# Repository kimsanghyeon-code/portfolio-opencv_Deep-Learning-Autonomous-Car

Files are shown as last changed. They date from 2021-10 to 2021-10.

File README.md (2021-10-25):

# 신경망을 이용한 자율주행차 구현
<hr>
  <h1> 구현 세부 내용 </h1>
<ol>
  <li> 듀얼쇼크4 페어링 후 'DataCollectionMain.py'실행하여 도로주행 </li>
  <li> 'Training.py'실행하여 주행하며 촬영한 이미지를 데이터화하여 저장하여 학습 </li>
  <li> 'RunMain.py'실행하여 자율주행 실시 </li>
</ol>
<hr>
  <h1> 필요 설치 툴 </h1>
opencv==4.4.0.44<br>
numpy==1.18.5<br>
pandas==1.1.3<br>
matplotlib==3.3.2<br>
scikit-learn==0.23.2<br>
tensorflow==2.3.1<br>
imgaug==0.4.0<br>

# 유튜브 링크 
https://www.youtube.com/channel/UCSaywzVMmYdEqYbF0HnaWPQ
<hr>

# Implementation of autonomous cars using neural networks.
<hr>
  <h1> Details of implementation </h1>
<ol>
  <li>After dualshock4 pairing, run 'DataCollectionMain.py' and drive on the road.</li>
  <li>Training by data-storing images taken while run 'Training.py'.</li>
  <li>Run 'RunMain.py' and drive on your own.</li>
</ol>
<hr>
  <h1>Required installation tool</h1>
opencv==4.4.0.44<br>
numpy==1.18.5<br>
pandas==1.1.3<br>
matplotlib==3.3.2<br>
scikit-learn==0.23.2<br>
tensorflow==2.3.1<br>
imgaug==0.4.0

# Youtube link
https://www.youtube.com/channel/UCSaywzVMmYdEqYbF0HnaWPQ

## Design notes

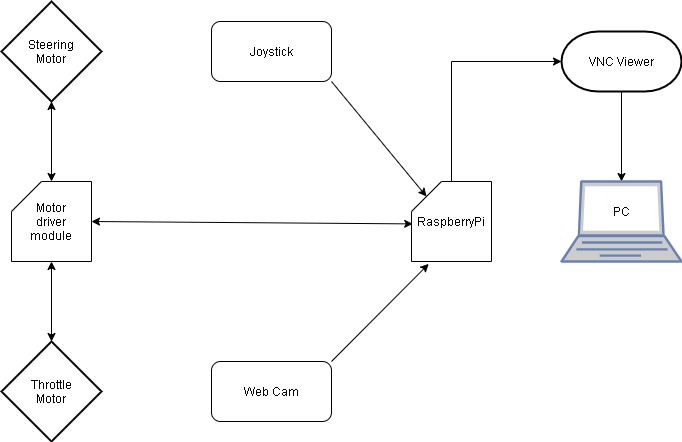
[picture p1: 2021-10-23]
the planning of hardware.jpg

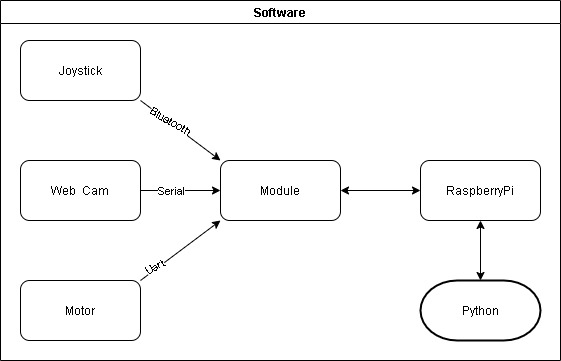
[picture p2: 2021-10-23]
the planning of software.jpg

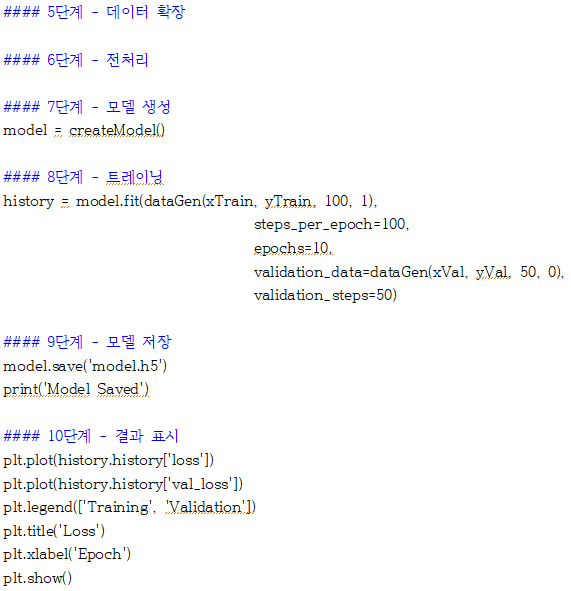
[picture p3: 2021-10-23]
Key code/training2.PNG

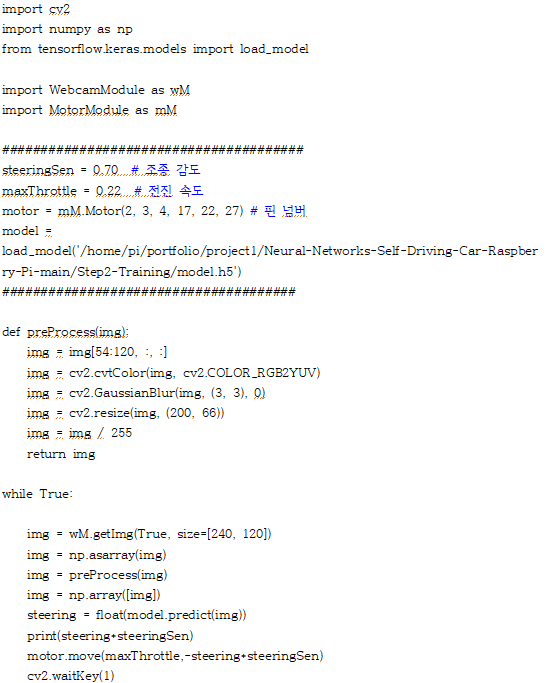
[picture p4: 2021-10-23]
Key code/RunMain.PNG

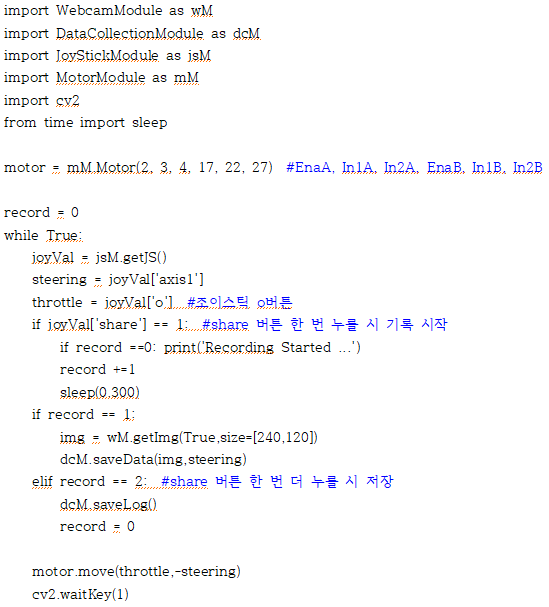
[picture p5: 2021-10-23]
Key code/DataCollectionMain.PNG

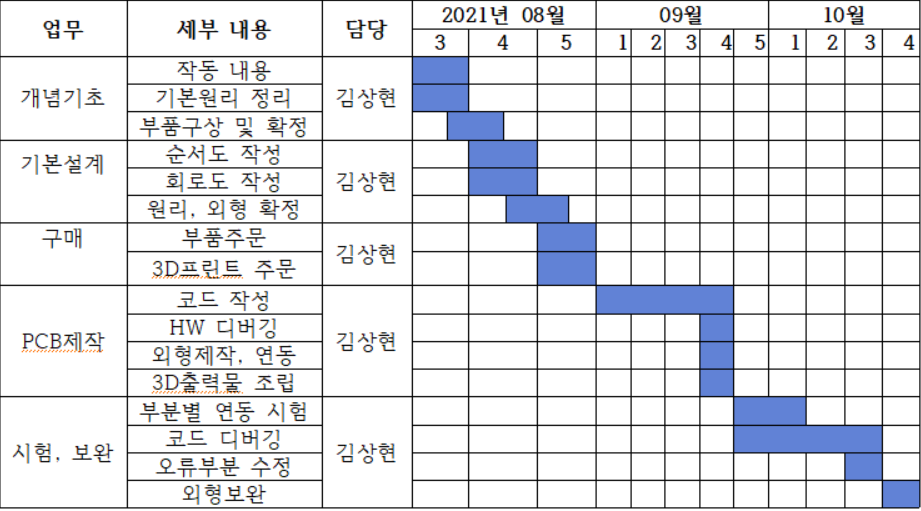
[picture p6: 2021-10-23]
gantt chart/gantt chart.PNG

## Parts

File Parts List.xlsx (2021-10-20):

NO | 수량 | 이름 | 요약 | 단가 | 금액 | 비고 | 구매처
1 | 1 | Raspberry Pi 4 기본 키트 | 라즈베리파이 4 (2GB) 기본 키트 | ₩76000 | ₩76000 | - | https://url.kr/bhwoyv
2 | 1 | RBP-018 | 라즈베리파이4 듀얼 쿨러 케이스 레드 | ₩13000 | ₩13000 | - | https://url.kr/hcrwje
3 | 4 | NP01S-220 | DC Motor(기어박스장착모터) | ₩1800 | ₩7200 | - | https://url.kr/8pzo3j
4 | 1 | SZH-EK001 | L298N (모터드라이버 모듈) | ₩2000 | ₩2000 | - | https://url.kr/rnwie4
5 | 3 | SZH-LP001 | 리튬 충전 배터리(18650) / 3.7V 2600mAh | ₩5000 | ₩15000 | - | https://url.kr/pveh75
6 | 1 | ND719 | 배터리 홀더(18650) 3구 / 2선 전원 15cm / 75mm*60mm*20mm | ₩1100 | ₩1100 | - | https://url.kr/ntd6ak
7 | 1 | 실습용납땜세트B | 인두기(30W) / 인두 스탠드 / 납흡입기 / 페이스트 / 납50g | ₩15000 | ₩15000 | - | https://url.kr/rfwu5k
8 | 1 | 점퍼용 단선 | 3색 점퍼용 단선 / 0.6mm(피복포함 약 1.3mm) / 길이 : 1m | ₩400 | ₩400 | - | https://url.kr/xp9iw7
9 | 1 | APC480 | ABKO APC480 SD Web Camera | ₩12900 | ₩12900 | - | https://url.kr/zs9xno
10 | 1 | 마스킹 테이프 | 흑색 / 50mm*40m | ₩6000 | ₩6000 | - | https://url.kr/oy58da
11 | 1 | Power bank | 보조배터리 / Pi 전원 공급용 / DC 5V,2A | ₩0 | ₩0 | 자체 재고 | -
12 | 1 | 차체 외형 | 3D 프린터 자체 제작 | ₩0 | ₩0 | - | -
13 | 4 | 바퀴 | 3D 프린터 자체 제작 | ₩0 | ₩0 | - | -
 |  |  |  | 합계 | ₩148600 | 부가세 별도

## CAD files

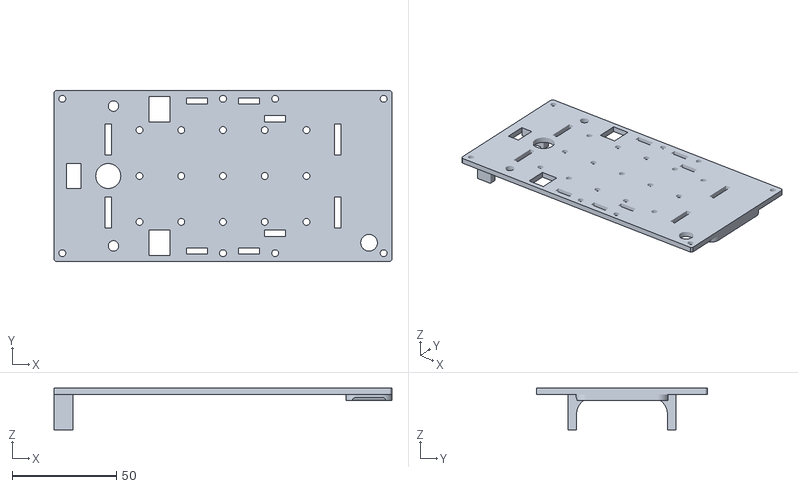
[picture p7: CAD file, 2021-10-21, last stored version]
rc-car/rc_car_top_plate.stl
162.0 x 82.0 x 20.0

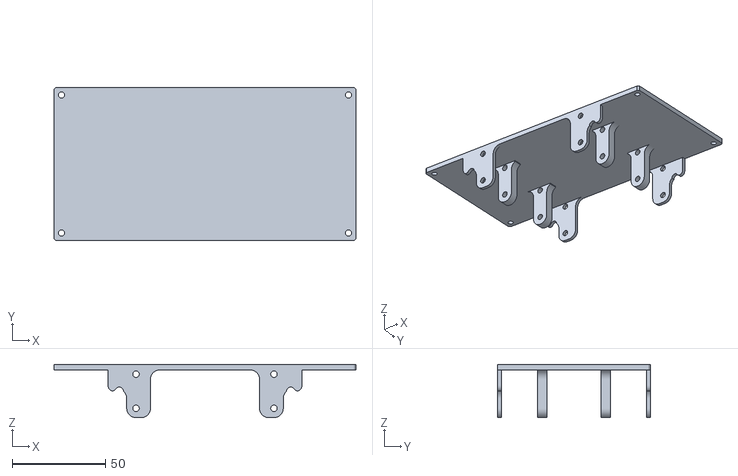
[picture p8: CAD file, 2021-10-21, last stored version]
rc-car/rc_car_bottom_plate.stl
162.0 x 82.0 x 28.6

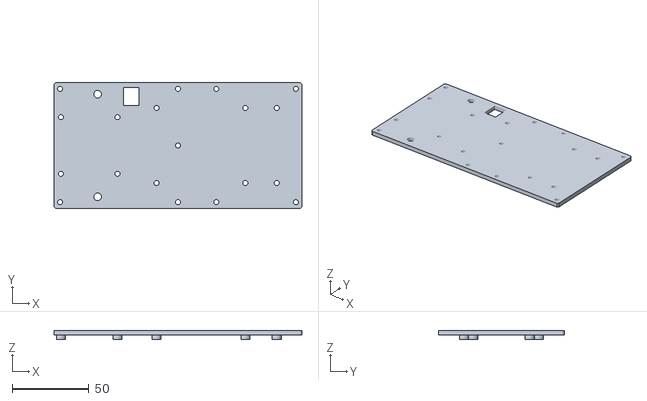
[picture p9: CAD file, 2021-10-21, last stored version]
rc-car/rc_car_middle_plate.stl
162.0 x 82.0 x 6.00

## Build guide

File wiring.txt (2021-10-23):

out1 = 좌측 앞바퀴 빨 + 뒷바퀴 검
out2 = 좌측 앞바퀴 검 + 뒷바퀴 빨
out3 = 우측 앞바퀴 빨 + 뒷바퀴 빨
out4 = 우측 앞바퀴 검 + 뒷바퀴 검

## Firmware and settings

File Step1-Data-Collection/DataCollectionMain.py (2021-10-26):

import WebcamModule as wM
import DataCollectionModule as dcM
import JoyStickModule as jsM
import MotorModule as mM
import cv2
from time import sleep

maxThrottle = 0.25
motor = mM.Motor(2, 3, 4, 17, 22, 27)

record = 0
while True:
    joyVal = jsM.getJS()
    steering = joyVal['axis1'] 
    throttle = joyVal['o']*maxThrottle  #조이스틱 o버튼
    if joyVal['share'] == 1:  #share 버튼 한 번 누를 시 기록 시작
        if record ==0: print('Recording Started ...')
        record +=1
        sleep(0.300)
    if record == 1:
        img = wM.getImg(True,size=[240,120])
        dcM.saveData(img,steering)
    elif record == 2:  #share 버튼 한 번 더 누를 시 저장
        dcM.saveLog()
        record = 0

    motor.move(throttle,-steering)
    cv2.waitKey(1)

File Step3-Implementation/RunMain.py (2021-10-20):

import cv2
import numpy as np
from tensorflow.keras.models import load_model

import WebcamModule as wM
import MotorModule as mM

#######################################
steeringSen = 0.70  # 조종 감도
maxThrottle = 0.22  # 전진 속도
motor = mM.Motor(2, 3, 4, 17, 22, 27) # 핀 넘버
model = load_model('/home/pi/portfolio/project1/Neural-Networks-Self-Driving-Car-Raspberry-Pi-main/Step2-Training/model.h5')
######################################

def preProcess(img):
    img = img[54:120, :, :]
    img = cv2.cvtColor(img, cv2.COLOR_RGB2YUV)
    img = cv2.GaussianBlur(img, (3, 3), 0)
    img = cv2.resize(img, (200, 66))
    img = img / 255
    return img

while True:

    img = wM.getImg(True, size=[240, 120])
    img = np.asarray(img)
    img = preProcess(img)
    img = np.array([img])
    steering = float(model.predict(img))
    print(steering*steeringSen)
    motor.move(maxThrottle,-steering*steeringSen)
    cv2.waitKey(1)
